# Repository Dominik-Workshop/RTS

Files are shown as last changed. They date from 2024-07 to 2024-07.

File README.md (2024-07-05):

# Linefollower

## Used tools:
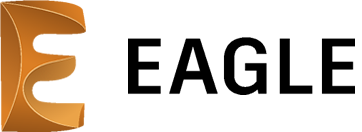
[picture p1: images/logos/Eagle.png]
 &nbsp;
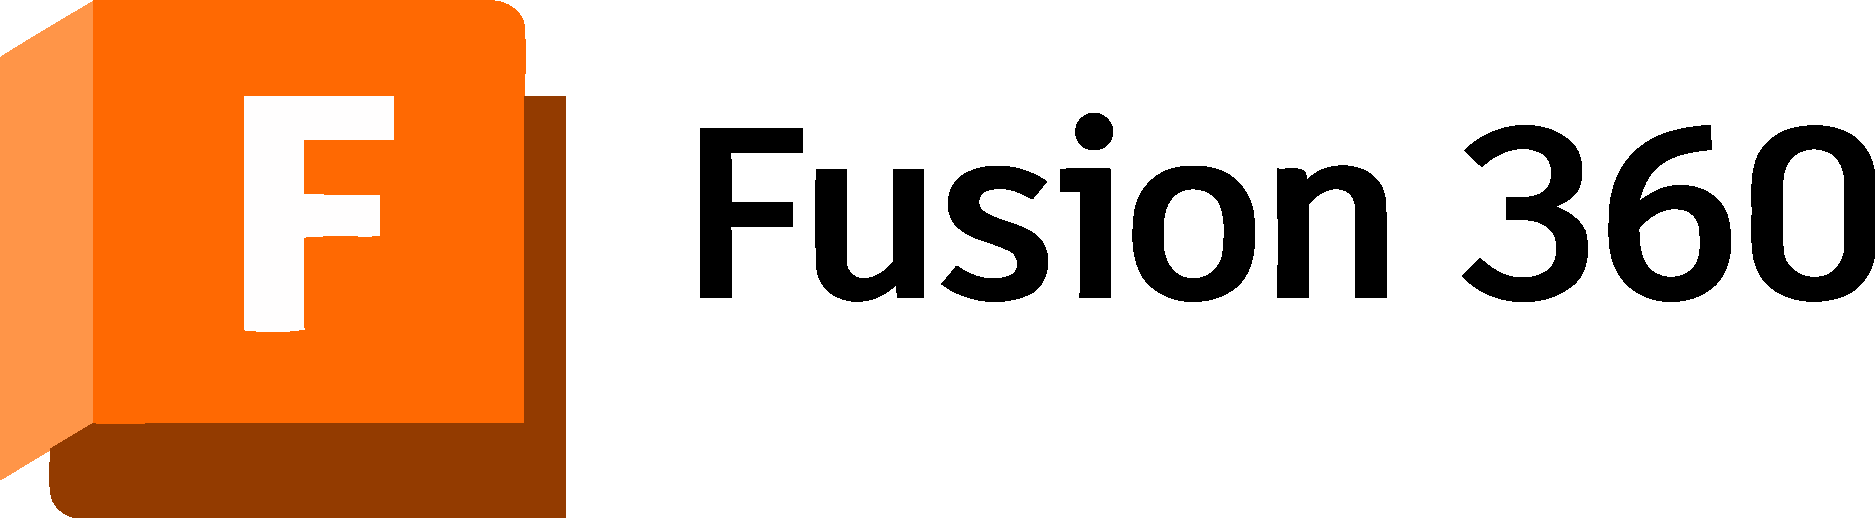
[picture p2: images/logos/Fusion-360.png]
 &nbsp;
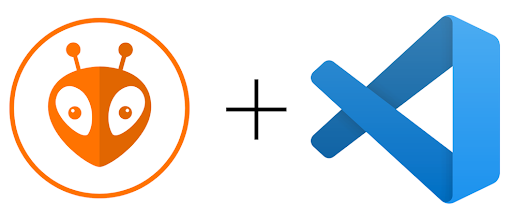
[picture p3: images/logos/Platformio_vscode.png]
 &nbsp;
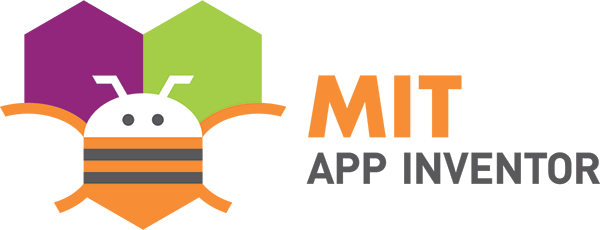
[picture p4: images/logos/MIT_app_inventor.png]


## Project overwiev
The Linefollower Robot is designed to autonomously navigate a track marked by a black line on a white surface. The goal is for the robot to complete the track as quickly as possible.
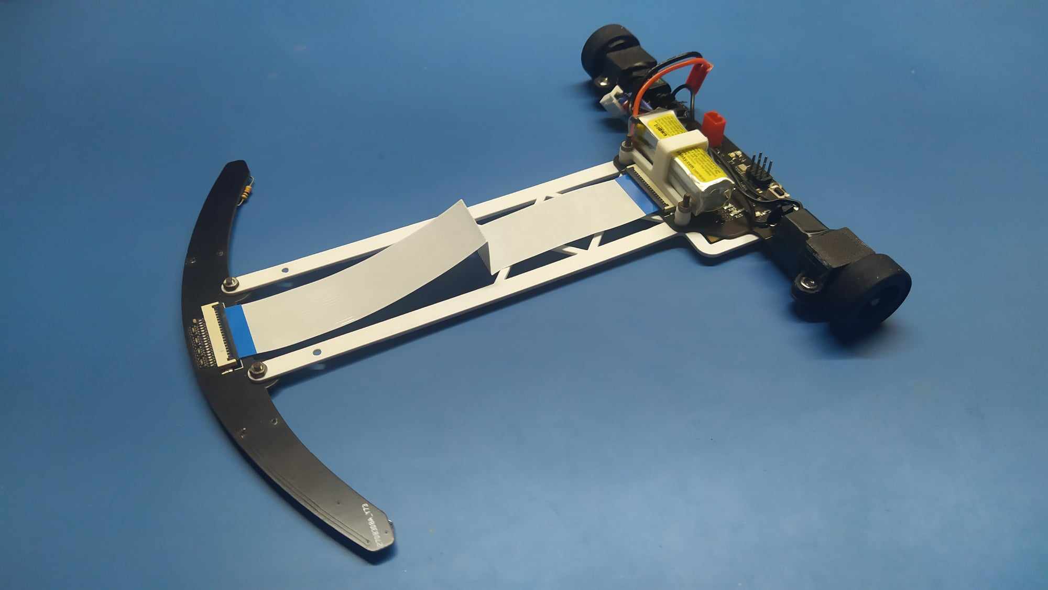
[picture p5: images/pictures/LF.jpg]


## Electronics

The robot incorporates 2 PCBs, which are connected via an FFC cable:
  - sensor board - contains 16 reflective sensors for line detection
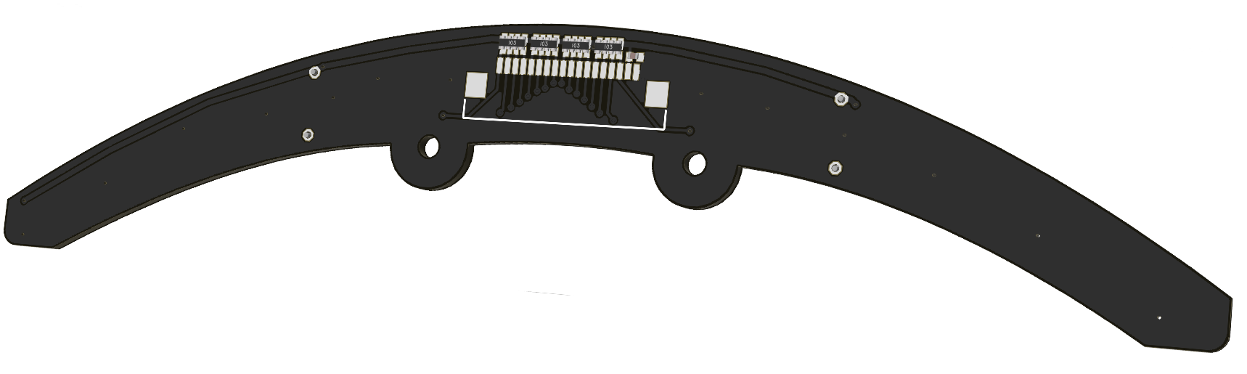
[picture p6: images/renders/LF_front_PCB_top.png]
  
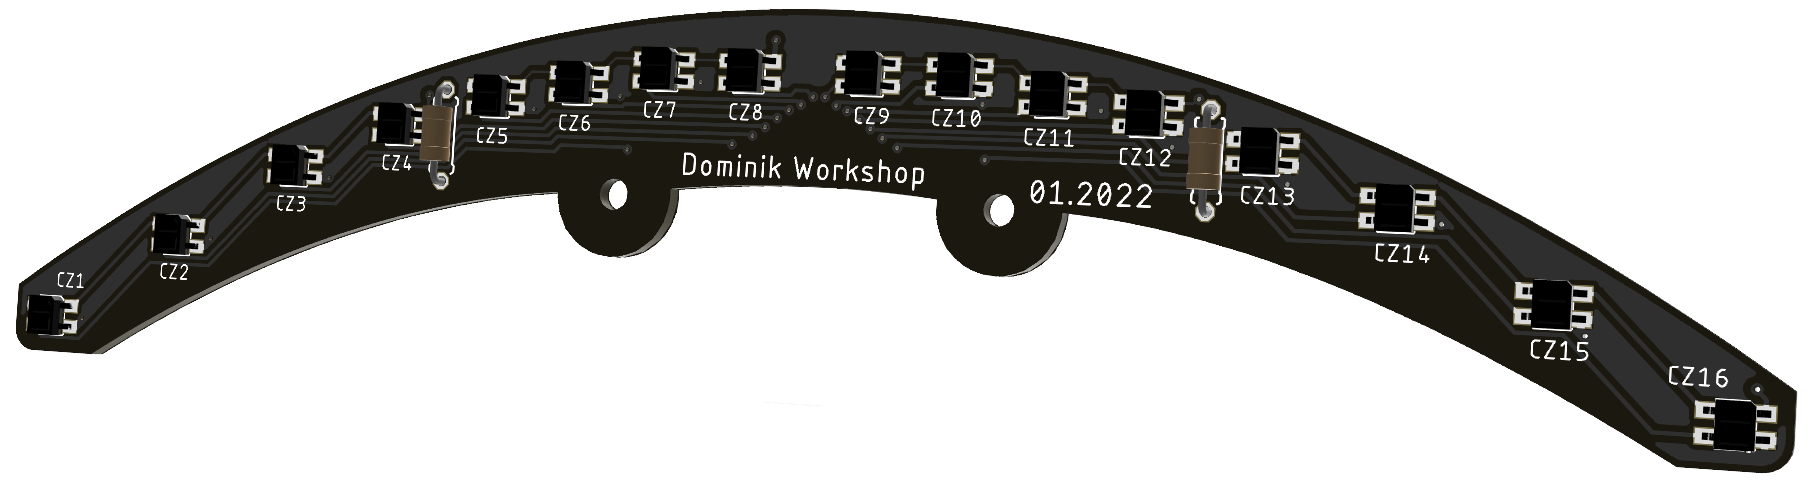
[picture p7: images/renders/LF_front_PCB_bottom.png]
  
  - main board 
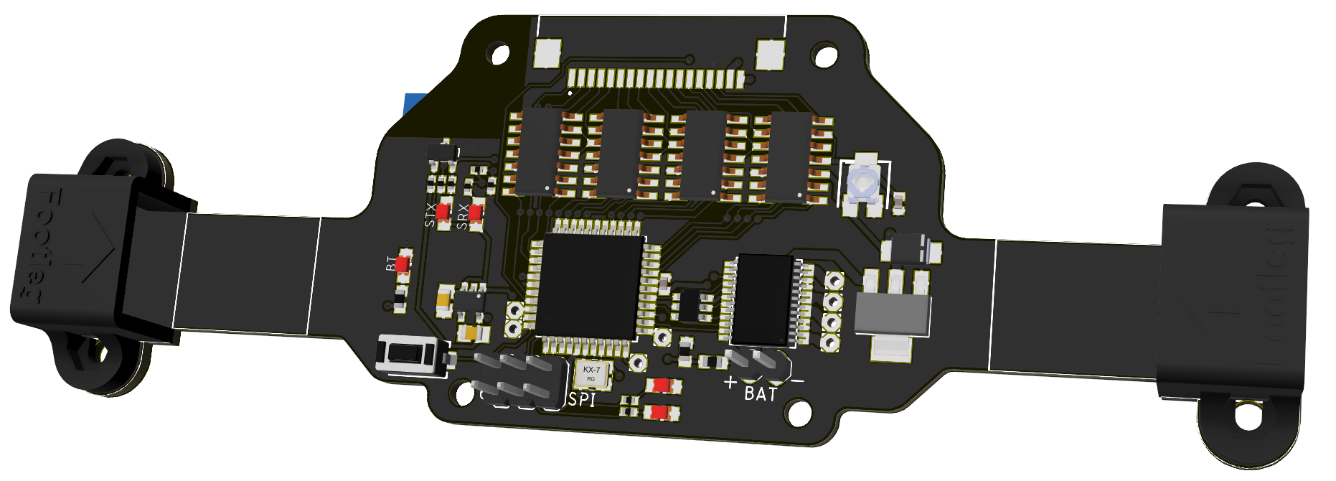
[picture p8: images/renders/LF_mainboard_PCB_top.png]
  
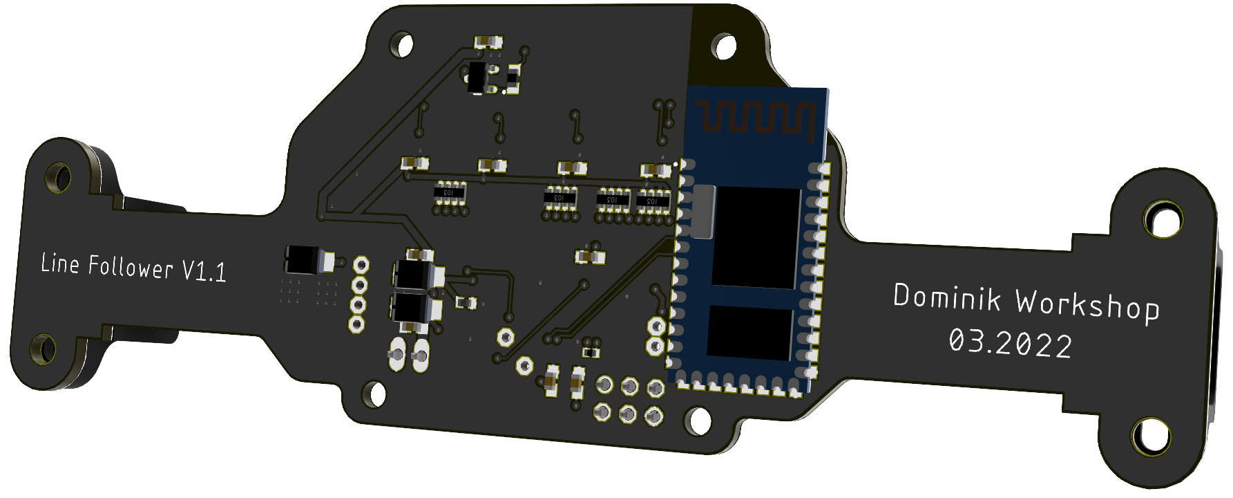
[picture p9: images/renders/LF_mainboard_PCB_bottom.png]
  

## Mechanical construction

The PCBs are mechanically joined with a lightweight 3D-printed connection bar. The motor and battery mounts are also 3D-printed.

## Android app
<p align="center">
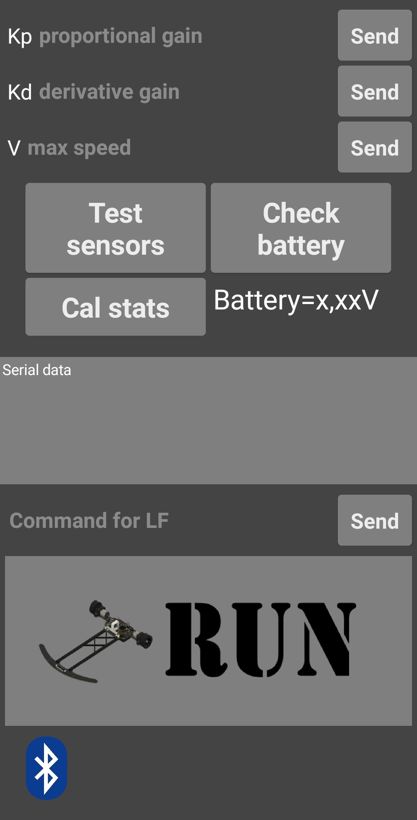
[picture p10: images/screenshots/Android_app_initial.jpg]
   &nbsp;&nbsp;
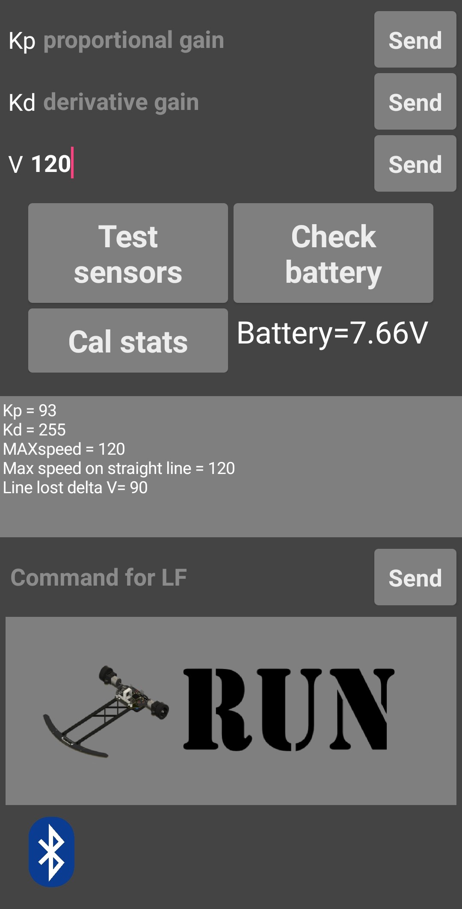
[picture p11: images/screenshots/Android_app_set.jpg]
  
</p>

## Uploading the code to the robot
If the microcontroller doesn't programm:
<details>
<summary>Click to view solution</summary>
Make sure that the fusebits are set as bellow:
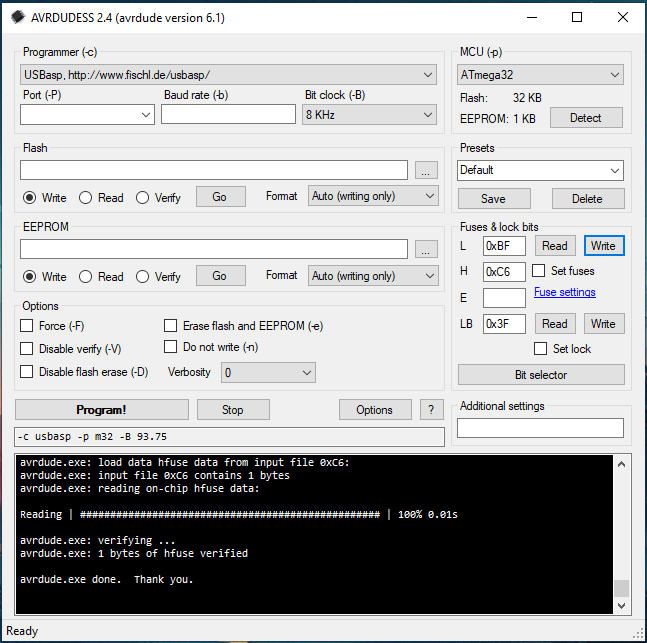
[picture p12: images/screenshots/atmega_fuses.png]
Fuse Bits Settings

</details>

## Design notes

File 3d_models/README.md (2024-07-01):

# 3D models

1. Wheel

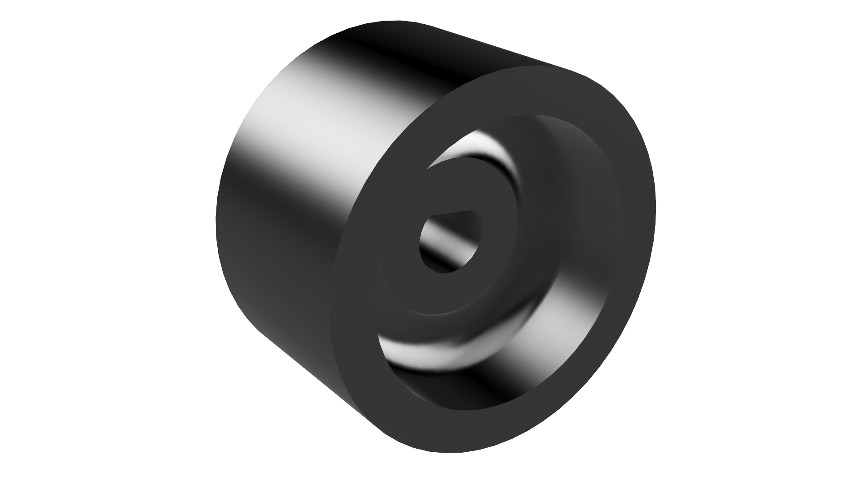
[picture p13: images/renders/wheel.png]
 

2. Battery holder

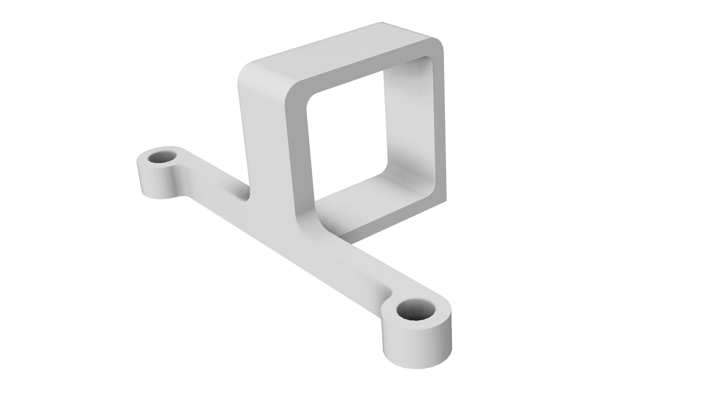
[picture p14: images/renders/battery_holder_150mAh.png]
 

3. Motor mount

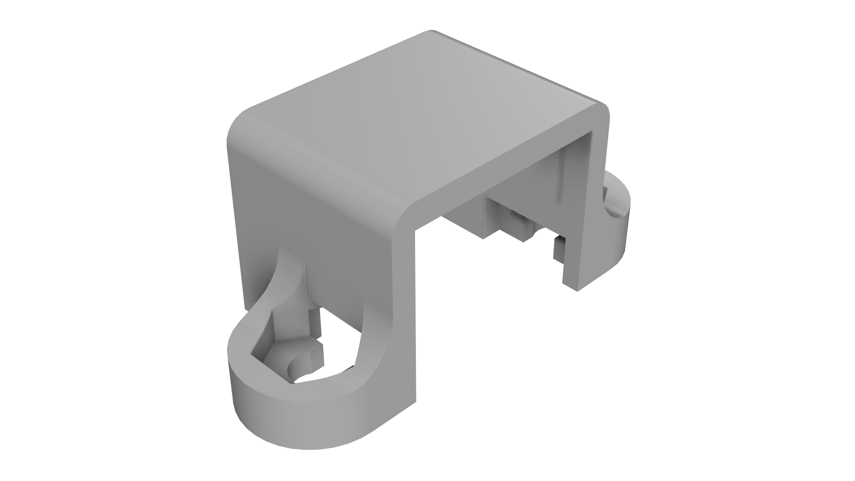
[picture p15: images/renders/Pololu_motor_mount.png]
 

4. Connection bar

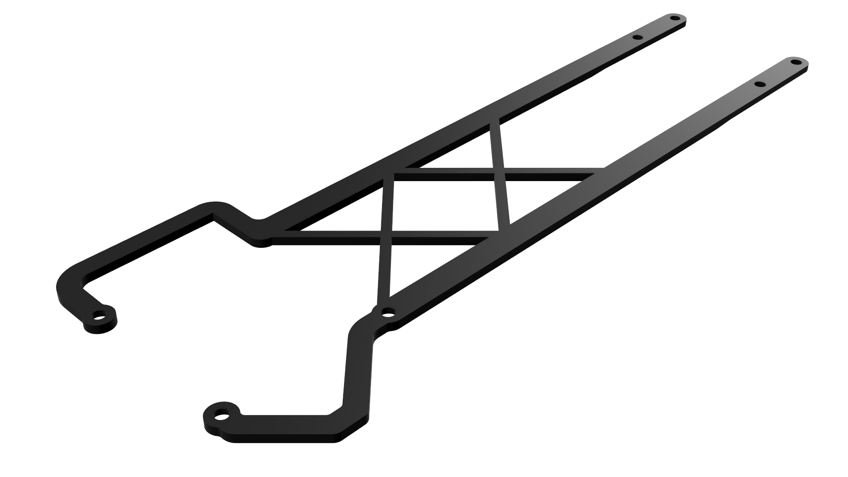
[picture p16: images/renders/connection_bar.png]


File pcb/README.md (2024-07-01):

## Main board

<p align="center">
  
</p>

## Sensor board

<p align="center">
  
</p>

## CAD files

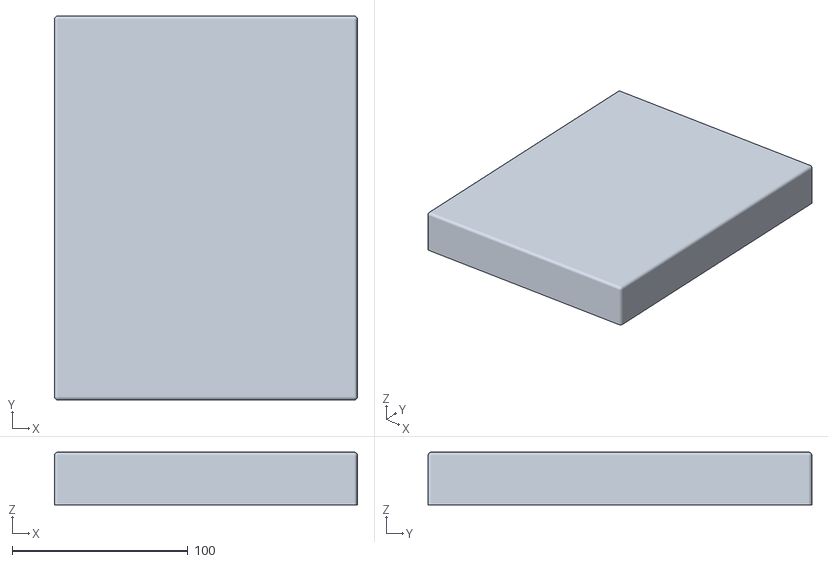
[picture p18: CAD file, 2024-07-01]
3d_models/LF_box_lid.stl
172.4 x 218.4 x 30.0

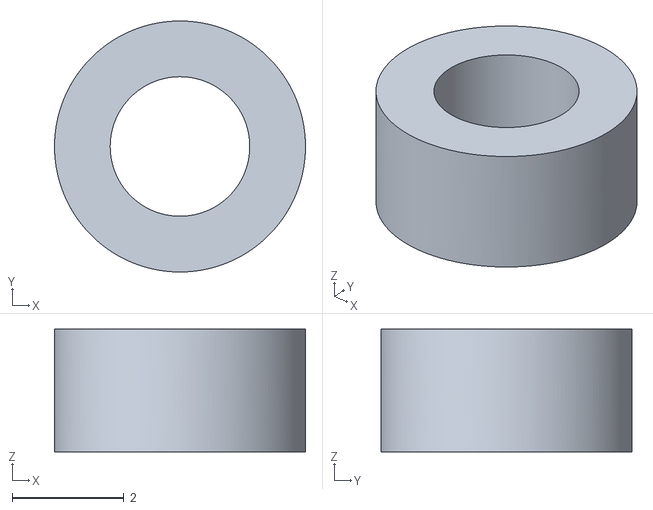
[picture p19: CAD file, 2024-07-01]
3d_models/LF_spacer.stl
4.50 x 4.50 x 2.20

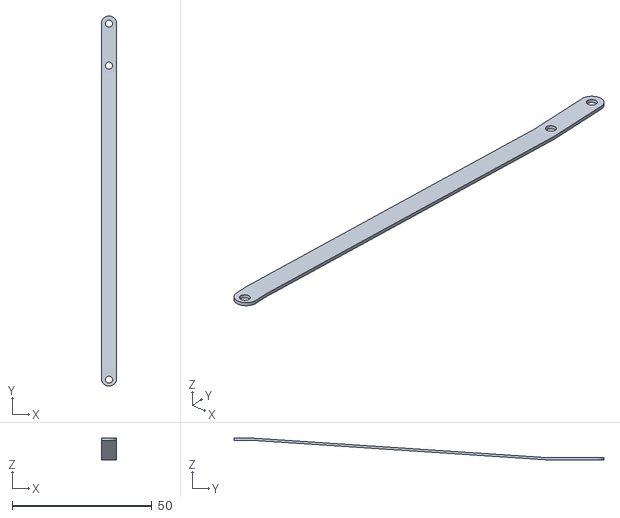
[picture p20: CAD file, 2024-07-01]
3d_models/LF_support_bar.stl
5.50 x 132.2 x 7.80

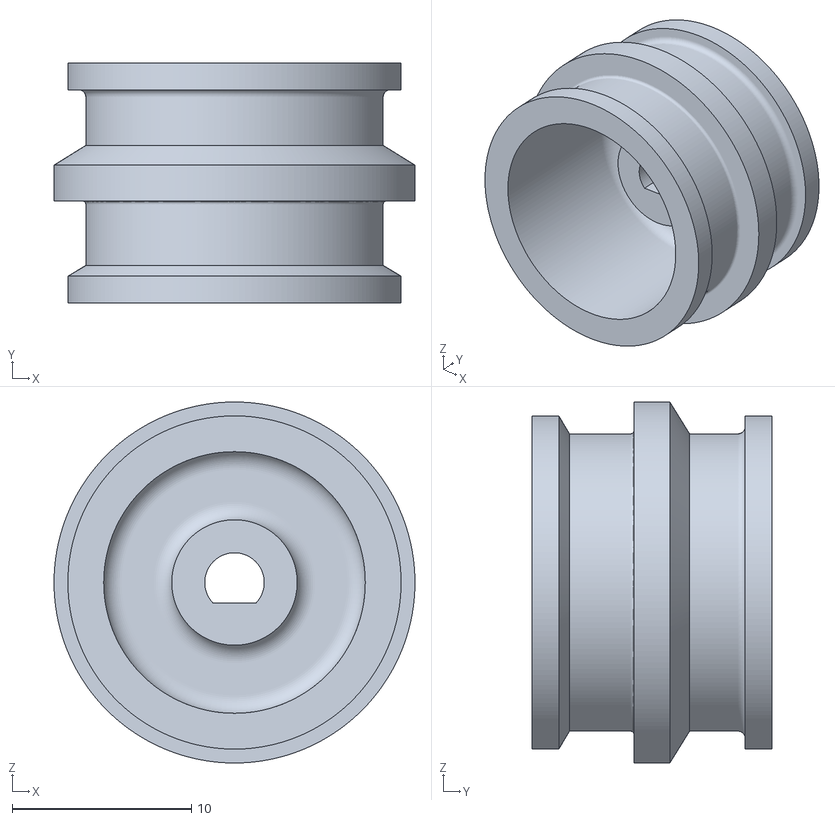
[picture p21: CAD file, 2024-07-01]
3d_models/LF_wheel_v2.stl
20.1 x 13.4 x 20.1

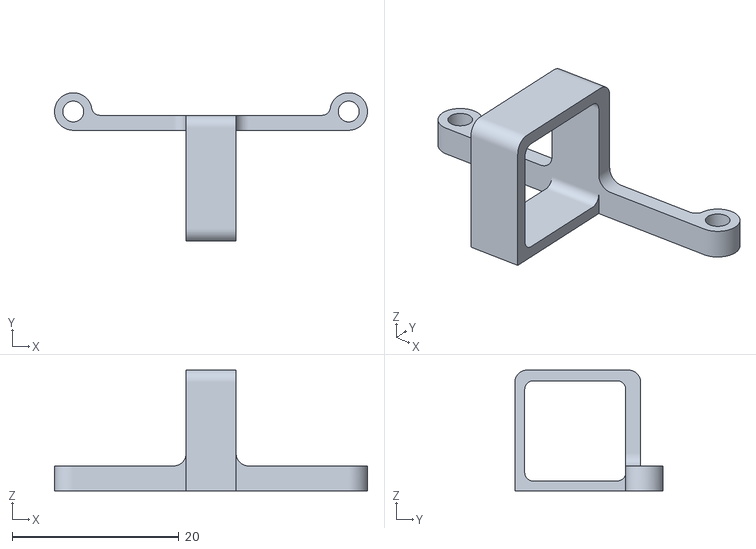
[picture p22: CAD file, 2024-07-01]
3d_models/LF_battery_holder_150mAh.stl
37.5 x 17.8 x 14.5

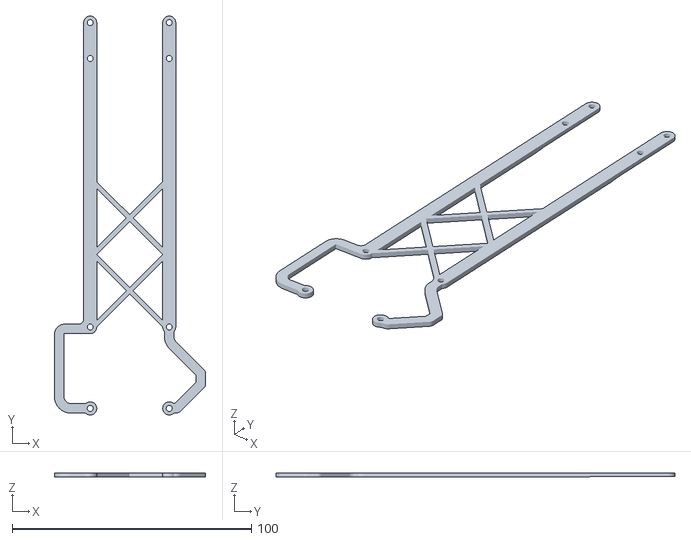
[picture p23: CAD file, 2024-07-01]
3d_models/LF_connection_bar.stl
63.2 x 166.8 x 1.80

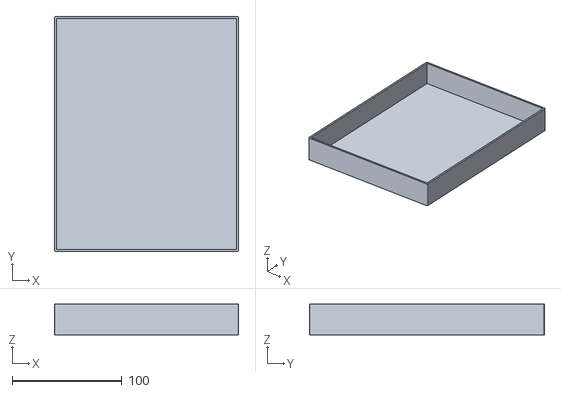
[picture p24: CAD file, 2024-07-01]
3d_models/LF_box_bottom.stl
168.0 x 214.0 x 28.0

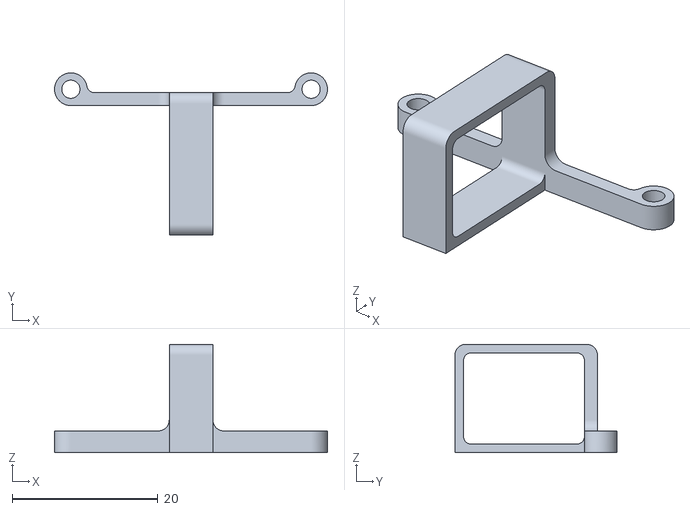
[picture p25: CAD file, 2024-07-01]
3d_models/LF_battery_holder_220mAh.stl
37.5 x 22.3 x 14.9

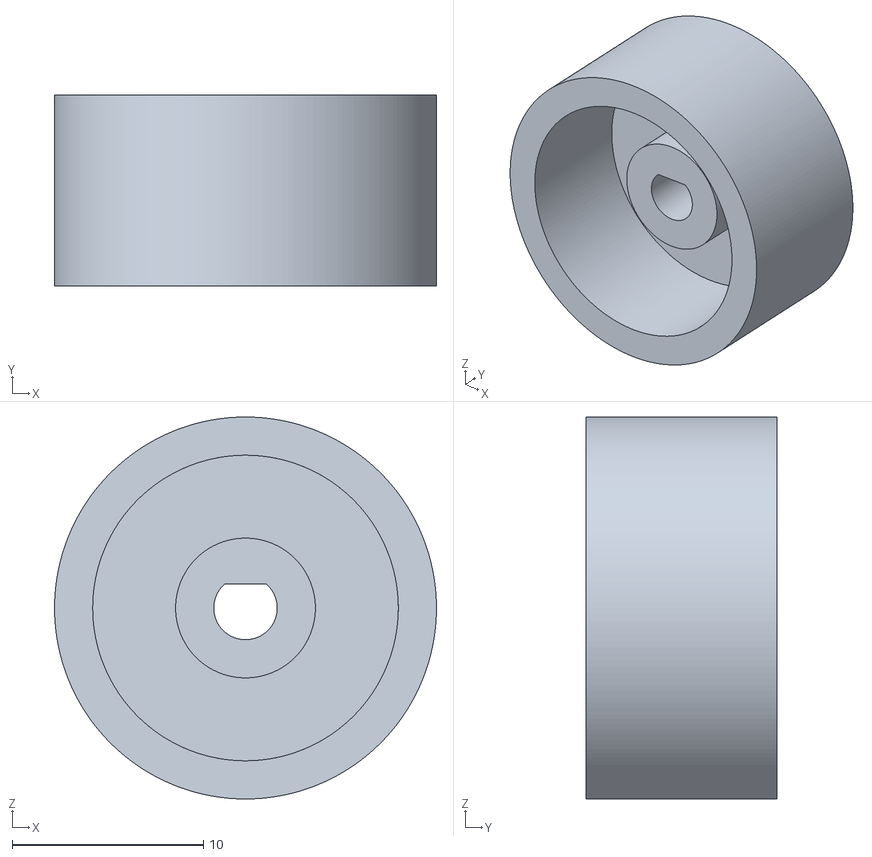
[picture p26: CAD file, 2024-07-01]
3d_models/LF_wheel.stl
20.0 x 10.0 x 20.0

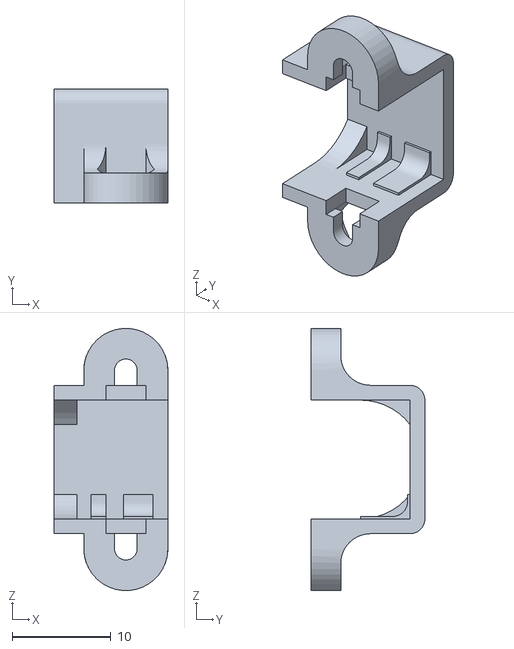
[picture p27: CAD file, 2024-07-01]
3d_models/LF_pololu_motor_holder.STL
11.5 x 11.5 x 26.5

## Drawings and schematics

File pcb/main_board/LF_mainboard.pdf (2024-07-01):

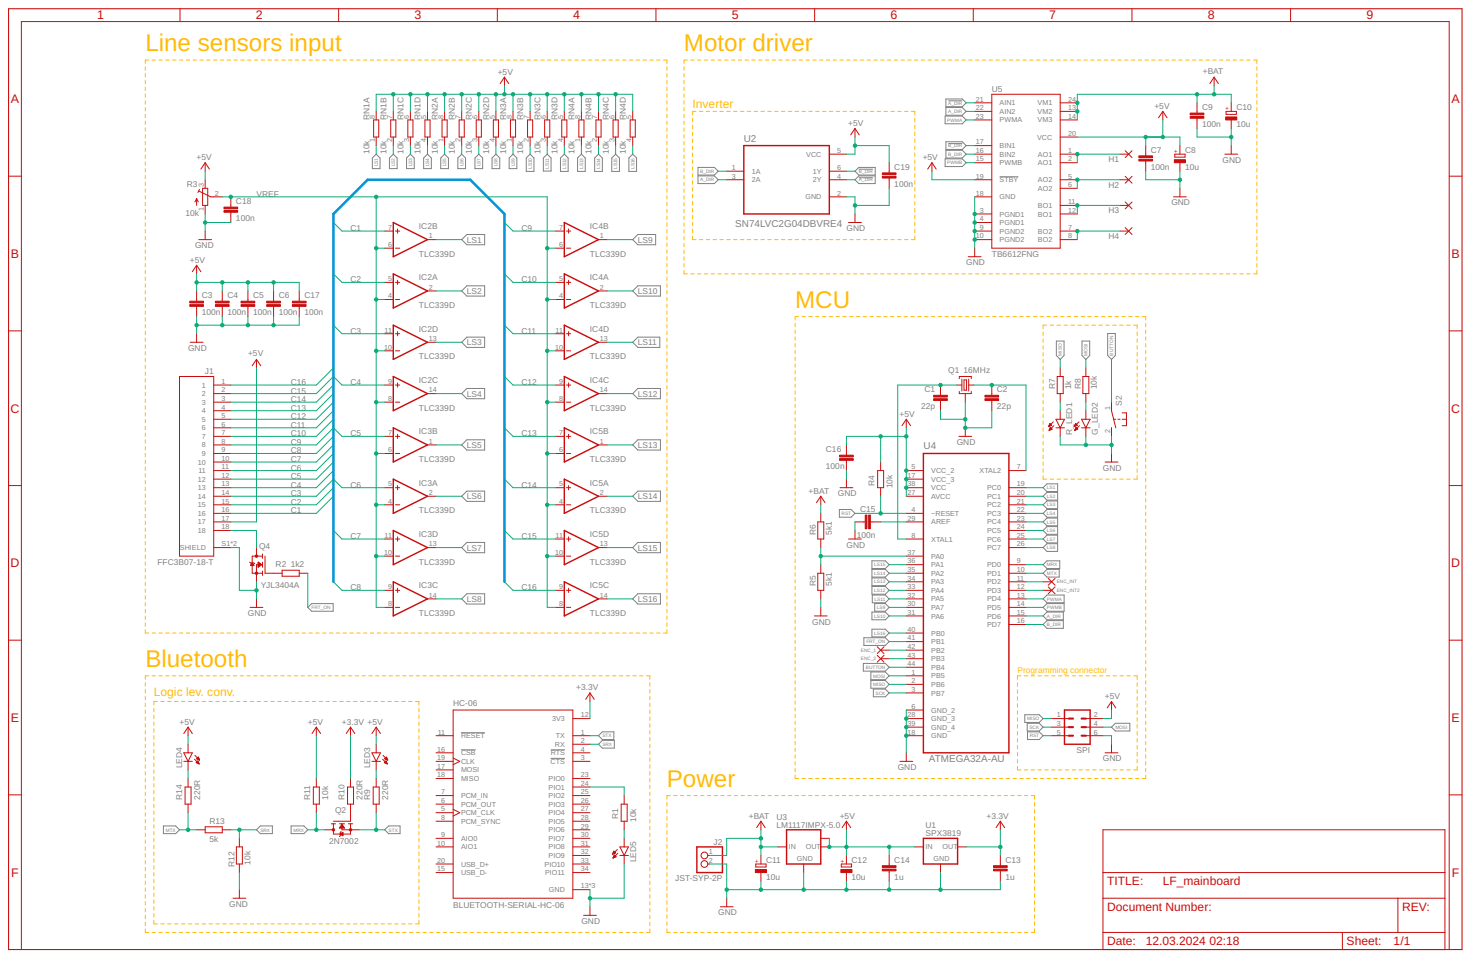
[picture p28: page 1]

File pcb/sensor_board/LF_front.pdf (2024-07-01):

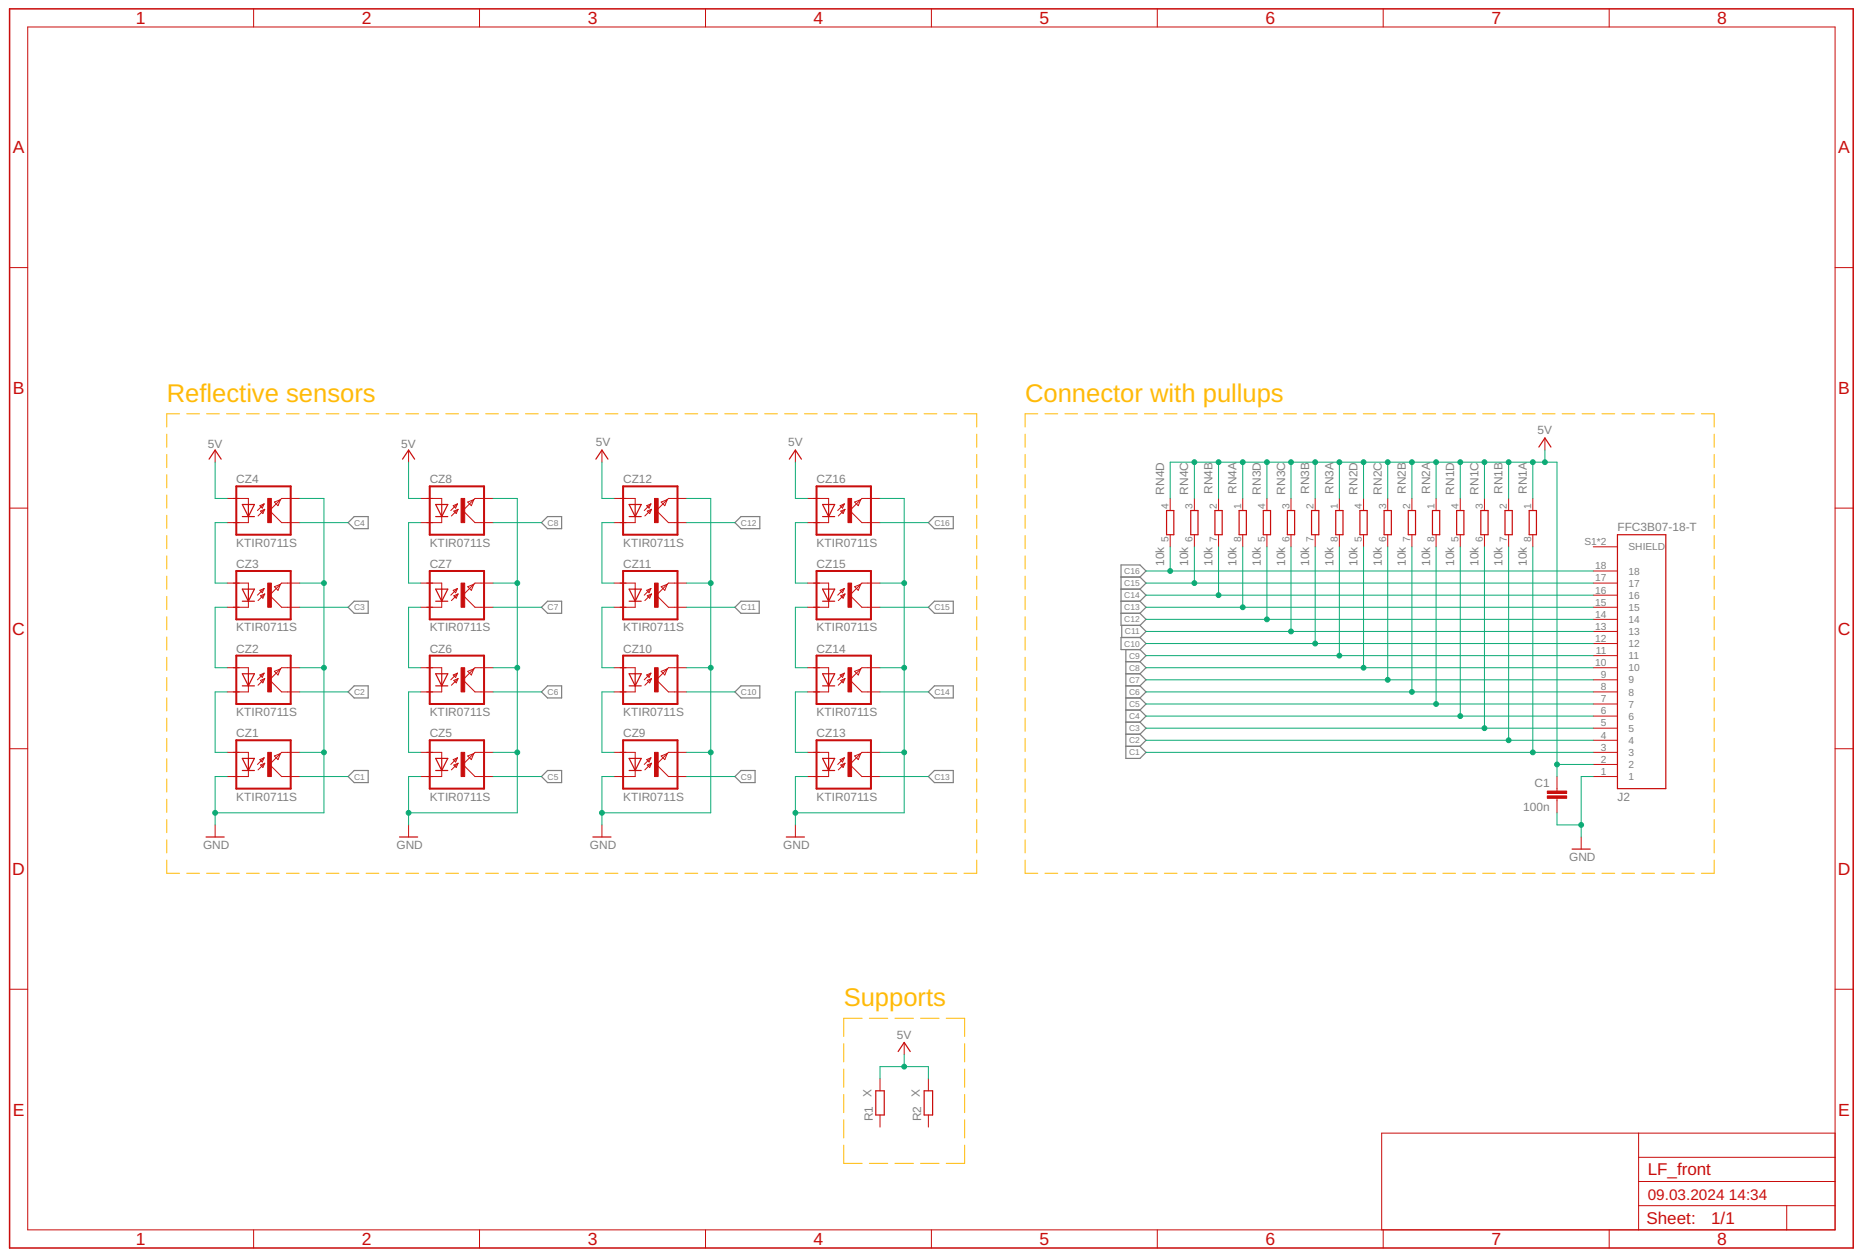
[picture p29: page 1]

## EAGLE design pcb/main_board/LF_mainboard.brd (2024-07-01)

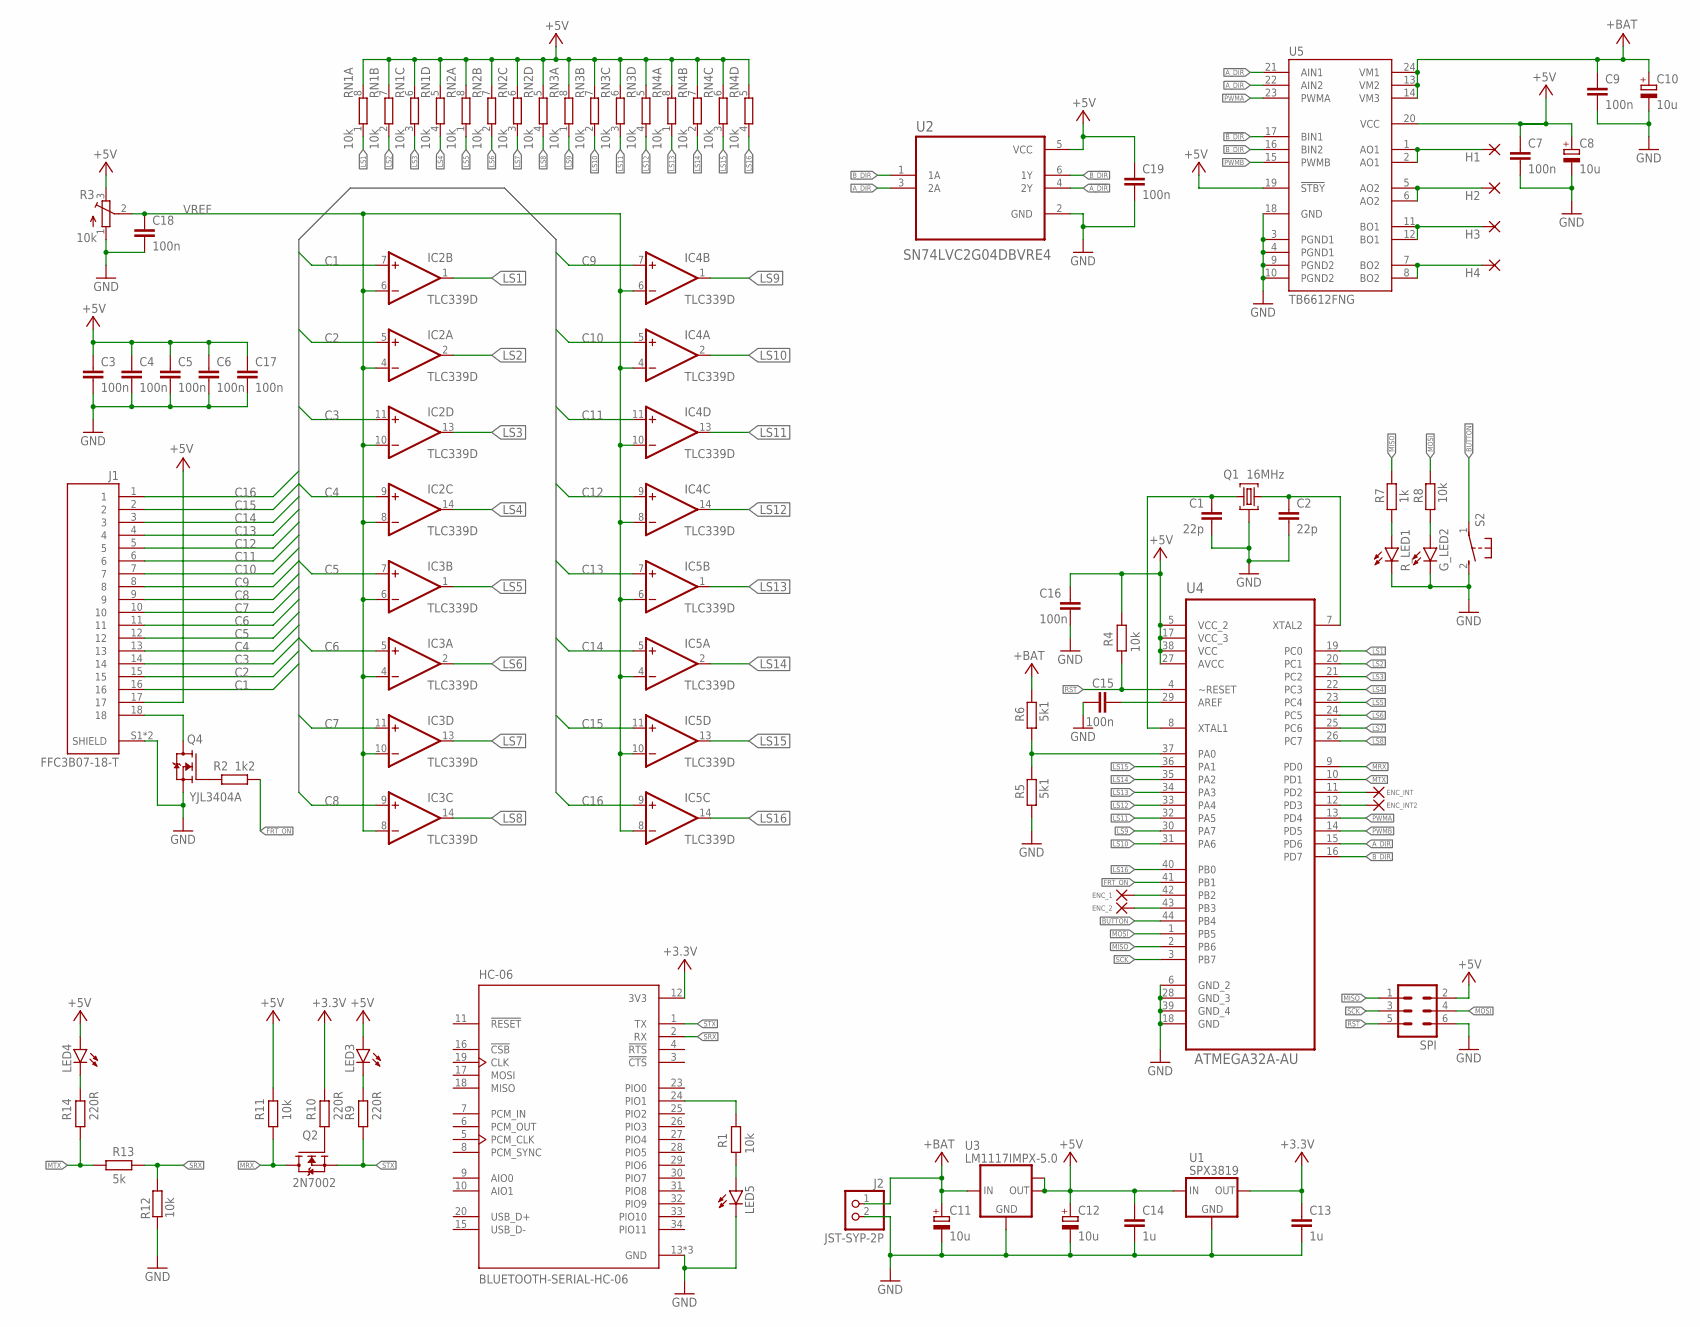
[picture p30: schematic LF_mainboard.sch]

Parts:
C1, C2: 22p; C0603
C3, C4, C5, C6, C7, C9, C15, C17: 100n; C0603
C8, C10, C11, C12: 10u; B/3528-21W
C13, C14: 1u; C0805
C16, C18, C19: 100n; C0402
ENC_2: 1,6/0,8
G_LED2: LEDCHIP-LED0805; CHIP-LED0805
H1, H2, H3, H4, H5, H6, H8: 1,6/0,8
HC-06: BLUETOOTH-SERIAL-HC-06; XCVR_BLUETOOTH-SERIAL-HC-06
IC2, IC3, IC4, IC5: TLC339D; SO14
J1: FFC3B07-18-T; GCT_FFC3B07-18-T
J2: JST-SYP-2P; 1X02
LED3, LED4, LED5: LEDCHIP-LED0805; CHIP-LED0805
Q1: 16MHz; CRYSTAL_3,4X2,7
Q2: 2N7002; SOT95P240X111-3N
Q4: YJL3404A; SOT95P240X111-3N
R1: 10k; R0603
R2: 1k2; R0603
R3: 10k; SM-42/43A
R4, R8, R11, R12: 10k; R0402
R5, R6: 5k1; R0603
R7: 1k; R0402
R9, R10, R14: 220R; R0402
R13: 5k; R0402
RN1, RN2, RN3, RN4: 10k; CAT16
R_LED1: LEDCHIP-LED0805; CHIP-LED0805
S2: DTSM-3
SPI: MA03-2
U1: SPX3819; SOT23-5
U2: SN74LVC2G04DBVRE4; SOT95P280X145-6N
U3: LM1117IMPX-5.0; SOT223
U4: ATMEGA32A-AU; QFP80P1200X1200X120-44N
U5: TB6612FNG; SSOP24

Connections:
!A_DIR: U2.4 (2Y), U5.21 (AIN1)
!B_DIR: U2.6 (1Y), U5.17 (BIN1)
+3.3V: C13.1, HC-06.12 (3V3), R10.2, U1.5 (OUT)
+5V: C3.1, C4.1, C5.1, C6.1, C7.1, C8.+, C12.+, C14.1, C16.1, C17.1, C19.1, IC2.3 (V+), IC3.3 (V+), IC4.3 (V+), IC5.3 (V+), J1.17, LED3.A, LED4.A, R3.3 (E), R4.2, R11.2, RN1.5 (2), RN1.6 (2), RN1.7 (2), RN1.8 (2), RN2.5 (2), RN2.6 (2), RN2.7 (2), RN2.8 (2), RN3.5 (2), RN3.6 (2), RN3.7 (2), RN3.8 (2), RN4.5 (2), RN4.6 (2), RN4.7 (2), RN4.8 (2), SPI.2, U1.1 (IN), U1.3 (IN), U2.5 (VCC), U3.2 (OUT), U3.TAB (OUT1), U4.5 (VCC_2), U4.17 (VCC_3), U4.27 (AVCC), U4.38 (VCC), U5.19 (!STBY), U5.20 (VCC)
+BAT: C9.1, C10.+, C11.+, J2.1, R6.2, U3.3 (IN), U5.13 (VM2), U5.14 (VM3), U5.24 (VM1)
AO: H1.1, U5.1 (AO1), U5.2 (AO1)
AO2: H2.1, U5.5 (AO2), U5.6 (AO2)
AREF: C15.2, U4.29 (AREF)
A_DIR: U2.3 (2A), U4.15 (PD6), U5.22 (AIN2)
BAT_MEAS: R5.2, R6.1, U4.37 (PA0)
BO1: H3.1, U5.11 (BO1), U5.12 (BO1)
BO2: H4.1, U5.7 (BO2), U5.8 (BO2)
BUTTON: S2.1, U4.44 (PB4)
B_DIR: U2.1 (1A), U4.16 (PD7), U5.16 (BIN2)
C1: IC2.7 (+IN), J1.16
C2: IC2.5 (+IN), J1.15
C3: IC2.11 (+IN), J1.14
C4: IC2.9 (+IN), J1.13
C5: IC3.7 (+IN), J1.12
C6: IC3.5 (+IN), J1.11
C7: IC3.11 (+IN), J1.10
C8: IC3.9 (+IN), J1.9
C9: IC4.7 (+IN), J1.8
C10: IC4.5 (+IN), J1.7
C11: IC4.11 (+IN), J1.6
C12: IC4.9 (+IN), J1.5
C13: IC5.7 (+IN), J1.4
C14: IC5.5 (+IN), J1.3
C15: IC5.11 (+IN), J1.2
C16: IC5.9 (+IN), J1.1
ENC_1: H8.1, U4.42 (PB2)
ENC_2: ENC_2.1, U4.43 (PB3)
ENC_INT: H5.1, U4.11 (PD2)
ENC_INT2: H6.1, U4.12 (PD3)
FRT_ON: R2.1, U4.41 (PB1)
GND: C1.2, C2.2, C3.2, C4.2, C5.2, C6.2, C7.2, C8.-, C9.2, C10.-, C11.-, C12.-, C13.2, C14.2, C15.1, C16.2, C17.2, C18.2, C19.2, G_LED2.C, HC-06.13 (GND), HC-06.21 (GND), HC-06.22 (GND), IC2.12 (V-), IC3.12 (V-), IC4.12 (V-), IC5.12 (V-), J1.S1 (SHIELD), J1.S2 (SHIELD), J2.2, LED5.C, Q1.GND (2), Q1.GND2 (2), Q4.2 (S), R3.1 (A), R5.1, R12.2, R_LED1.C, S2.2, SPI.6, U1.2 (GND), U2.2 (GND), U3.1 (GND), U4.6 (GND_2), U4.18 (GND), U4.28 (GND_3), U4.39 (GND_4), U5.3 (PGND1), U5.4 (PGND1), U5.9 (PGND2), U5.10 (PGND2), U5.18 (GND)
LED1: R7.1, R_LED1.A
LED2: G_LED2.A, R8.1
LS1: IC2.1 (OUT), RN1.1, U4.19 (PC0)
LS2: IC2.2 (OUT), RN1.2 (1), U4.20 (PC1)
LS3: IC2.13 (OUT), RN1.3 (1), U4.21 (PC2)
LS4: IC2.14 (OUT), RN1.4 (1), U4.22 (PC3)
LS5: IC3.1 (OUT), RN2.1, U4.23 (PC4)
LS6: IC3.2 (OUT), RN2.2 (1), U4.24 (PC5)
LS7: IC3.13 (OUT), RN2.3 (1), U4.25 (PC6)
LS8: IC3.14 (OUT), RN2.4 (1), U4.26 (PC7)
LS9: IC4.1 (OUT), RN3.1, U4.30 (PA7)
LS10: IC4.2 (OUT), RN3.2 (1), U4.31 (PA6)
LS11: IC4.13 (OUT), RN3.3 (1), U4.32 (PA5)
LS12: IC4.14 (OUT), RN3.4 (1), U4.33 (PA4)
LS13: IC5.1 (OUT), RN4.1, U4.34 (PA3)
LS14: IC5.2 (OUT), RN4.2 (1), U4.35 (PA2)
LS15: IC5.13 (OUT), RN4.3 (1), U4.36 (PA1)
LS16: IC5.14 (OUT), RN4.4 (1), U4.40 (PB0)
MISO: R7.2, SPI.1, U4.2 (PB6)
MOSI: R8.2, SPI.4, U4.1 (PB5)
MRX: Q2.3 (D), R11.1, U4.9 (PD0)
MTX: R13.1, R14.1, U4.10 (PD1)
unnamed: C1.1, Q1.CRST1 (1), U4.8 (XTAL1)
unnamed: C2.1, Q1.CRST2 (3), U4.7 (XTAL2)
unnamed: J1.18, Q4.3 (D)
unnamed: Q4.1 (G), R2.2
unnamed: HC-06.24 (PIO1), R1.2
unnamed: Q2.1 (G), R10.1
unnamed: LED4.C, R14.2
unnamed: LED3.C, R9.2
unnamed: LED5.A, R1.1
PWMA: U4.13 (PD4), U5.23 (PWMA)
PWMB: U4.14 (PD5), U5.15 (PWMB)
RST: R4.1, SPI.5, U4.4 (~RESET)
SCK: SPI.3, U4.3 (PB7)
SRX: HC-06.2 (RX), R12.1, R13.2
STX: HC-06.1 (TX), Q2.2 (S), R9.1
VREF: C18.1, IC2.4 (-IN), IC2.6 (-IN), IC2.8 (-IN), IC2.10 (-IN), IC3.4 (-IN), IC3.6 (-IN), IC3.8 (-IN), IC3.10 (-IN), IC4.4 (-IN), IC4.6 (-IN), IC4.8 (-IN), IC4.10 (-IN), IC5.4 (-IN), IC5.6 (-IN), IC5.8 (-IN), IC5.10 (-IN), R3.2 (S)

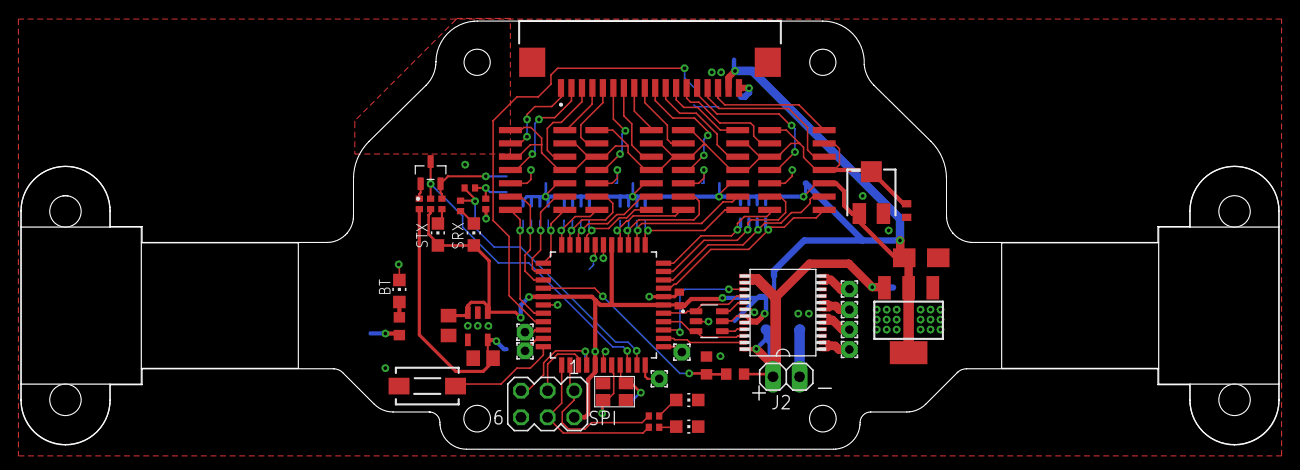
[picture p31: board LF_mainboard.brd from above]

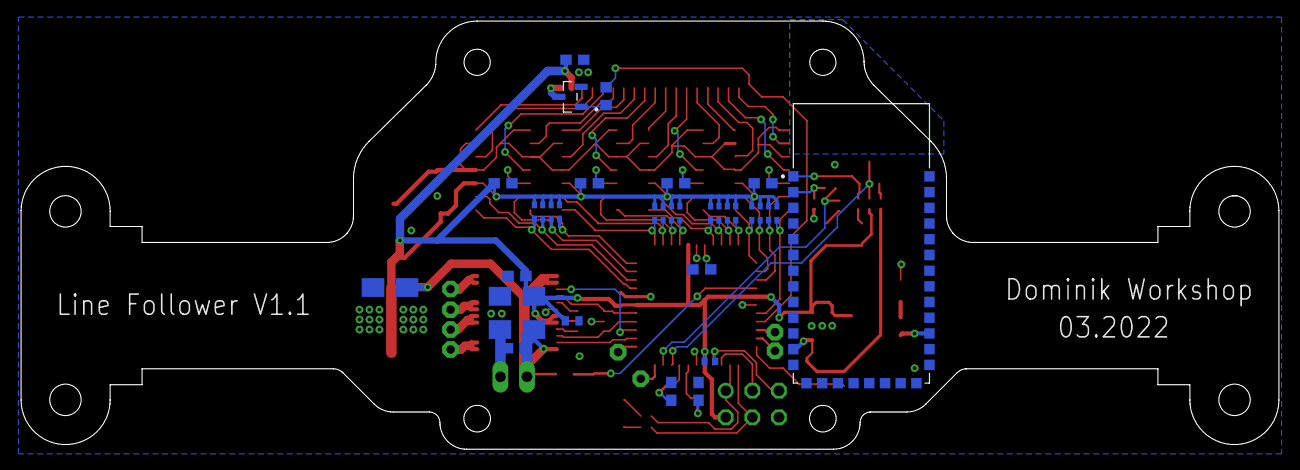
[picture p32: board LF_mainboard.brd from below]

Board: 2 copper layers, 120.1 x 40.9 mm, 69 parts (22 on the bottom side), 74 nets.

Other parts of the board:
U$1, U$2: HP_NM

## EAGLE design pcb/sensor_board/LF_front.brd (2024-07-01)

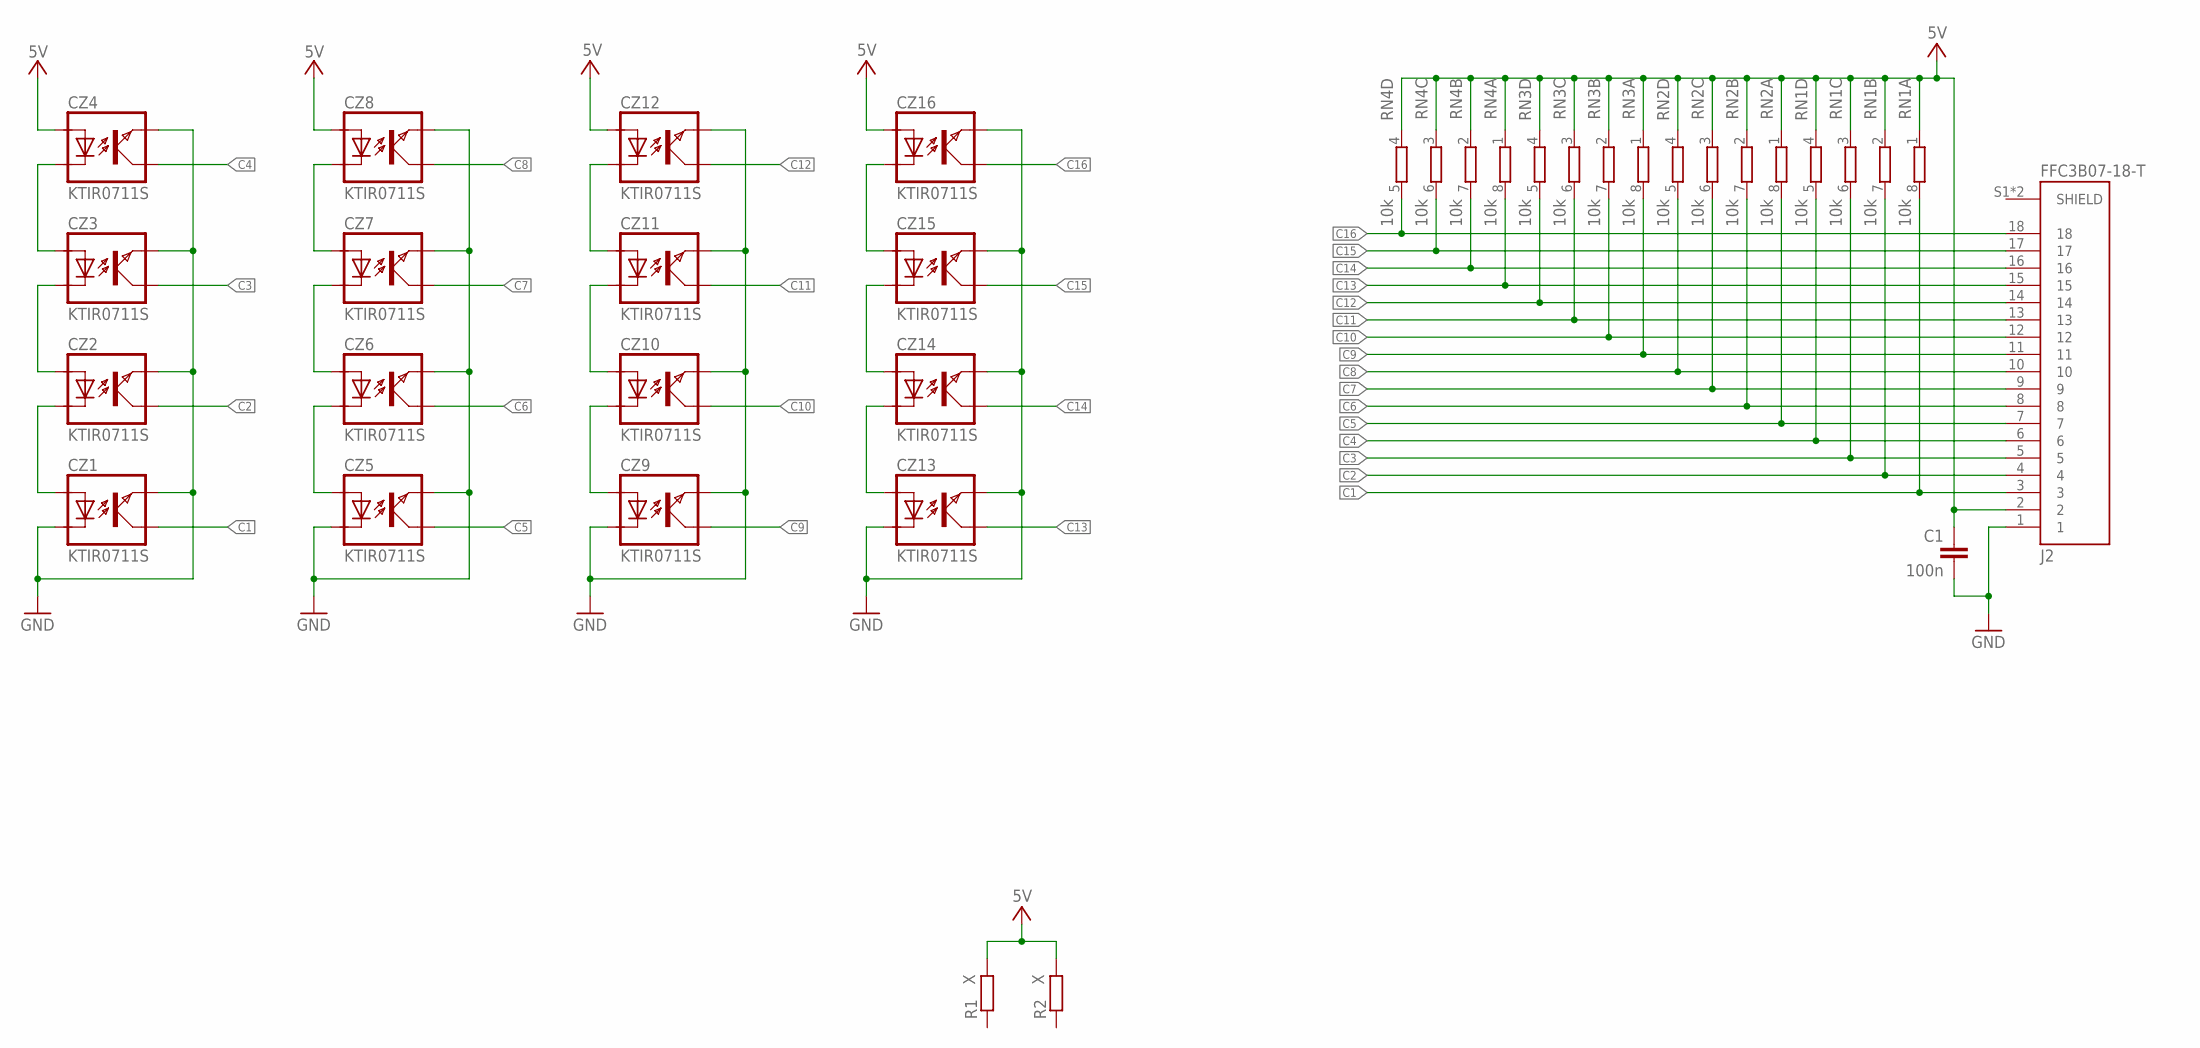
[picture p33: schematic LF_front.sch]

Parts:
C1: 100n; C0402
CZ1, CZ2, CZ3, CZ4, CZ5, CZ6, CZ7, CZ8, CZ9, CZ10, CZ11, CZ12, CZ13, CZ14, CZ15, CZ16: KTIR0711S; TOP
J2: FFC3B07-18-T; GCT_FFC3B07-18-T
R1, R2: X; 0207/7
RN1, RN2, RN3, RN4: 10k; EXB38V

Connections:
5V: C1.2, CZ4.ANODA, CZ8.ANODA, CZ12.ANODA, CZ16.ANODA, J2.2, R1.2, R2.2, RN1.1, RN1.2 (1), RN1.3 (1), RN1.4 (1), RN2.1, RN2.2 (1), RN2.3 (1), RN2.4 (1), RN3.1, RN3.2 (1), RN3.3 (1), RN3.4 (1), RN4.1, RN4.2 (1), RN4.3 (1), RN4.4 (1)
C1: CZ1.KOLEKTOR, J2.3, RN1.8 (2)
C2: CZ2.KOLEKTOR, J2.4, RN1.7 (2)
C3: CZ3.KOLEKTOR, J2.5, RN1.6 (2)
C4: CZ4.KOLEKTOR, J2.6, RN1.5 (2)
C5: CZ5.KOLEKTOR, J2.7, RN2.8 (2)
C6: CZ6.KOLEKTOR, J2.8, RN2.7 (2)
C7: CZ7.KOLEKTOR, J2.9, RN2.6 (2)
C8: CZ8.KOLEKTOR, J2.10, RN2.5 (2)
C9: CZ9.KOLEKTOR, J2.11, RN3.8 (2)
C10: CZ10.KOLEKTOR, J2.12, RN3.7 (2)
C11: CZ11.KOLEKTOR, J2.13, RN3.6 (2)
C12: CZ12.KOLEKTOR, J2.14, RN3.5 (2)
C13: CZ13.KOLEKTOR, J2.15, RN4.8 (2)
C14: CZ14.KOLEKTOR, J2.16, RN4.7 (2)
C15: CZ15.KOLEKTOR, J2.17, RN4.6 (2)
C16: CZ16.KOLEKTOR, J2.18, RN4.5 (2)
GND: C1.1, CZ1.EMITER, CZ1.KATODA, CZ2.EMITER, CZ3.EMITER, CZ4.EMITER, CZ5.EMITER, CZ5.KATODA, CZ6.EMITER, CZ7.EMITER, CZ8.EMITER, CZ9.EMITER, CZ9.KATODA, CZ10.EMITER, CZ11.EMITER, CZ12.EMITER, CZ13.EMITER, CZ13.KATODA, CZ14.EMITER, CZ15.EMITER, CZ16.EMITER, J2.1
unnamed: CZ1.ANODA, CZ2.KATODA
unnamed: CZ2.ANODA, CZ3.KATODA
unnamed: CZ3.ANODA, CZ4.KATODA
unnamed: CZ15.ANODA, CZ16.KATODA
unnamed: CZ14.ANODA, CZ15.KATODA
unnamed: CZ13.ANODA, CZ14.KATODA
unnamed: CZ11.ANODA, CZ12.KATODA
unnamed: CZ10.ANODA, CZ11.KATODA
unnamed: CZ9.ANODA, CZ10.KATODA
unnamed: CZ5.ANODA, CZ6.KATODA
unnamed: CZ6.ANODA, CZ7.KATODA
unnamed: CZ7.ANODA, CZ8.KATODA

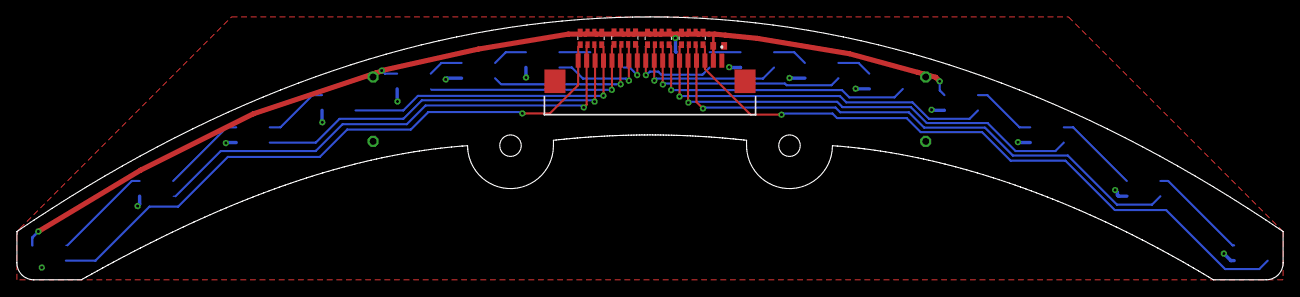
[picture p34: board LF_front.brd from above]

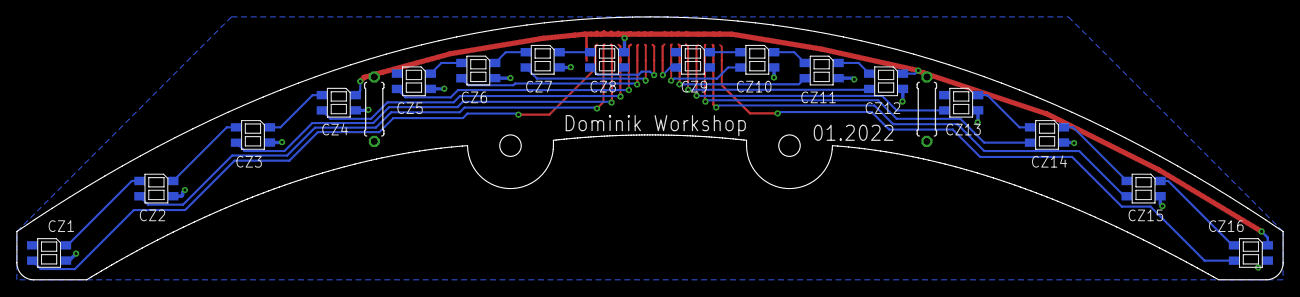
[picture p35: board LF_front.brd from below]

Board: 2 copper layers, 149.9 x 31.1 mm, 24 parts (18 on the bottom side), 30 nets.

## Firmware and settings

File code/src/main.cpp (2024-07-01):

/**
 * @file main.cpp
 * @author Dominik Workshop
 * @brief 
 * @version 0.1
 * @date 2024-03-30
 * 
 * @copyright Copyright (c) 2024
 * 
 */

#include <Arduino.h>

#include "linefollower.hh"

int main() {

  init();   // Arduino function, initializes peripherals

  Serial.begin(9600);

  Linefollower linefollower;

  while(1){
    linefollower.battery.checkVoltage();
    if(digitalRead(BUTTON) == LOW)
      linefollower.spinWheelsForCleaning();

    if(Serial.available()>0){
      char data = Serial.read();
      switch(data){
        case 'B':
          linefollower.battery.sendVoltage();
          break;
        case 't': 
          linefollower.lineSensors.test();
          break;
        case 'D': 
          linefollower.driveOnLine();
          break;
        case 'c':
          linefollower.calibration();
          break;  
        case 0x0A:
          break;
        case 0x0D:
          break;
        default : 
          Serial.println("Incorrect option");
          break;
        }
    }
  }
} 

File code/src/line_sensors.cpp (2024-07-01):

/**
 * @file line_sensors.cpp
 * @author Dominik Workshop
 * @brief 
 * @version 0.1
 * @date 2024-03-30
 * 
 * @copyright Copyright (c) 2024
 * 
 */

#include "line_sensors.hh"

LineSensors::LineSensors(){
  pinMode(FRONT_POWER, OUTPUT);
  digitalWrite(FRONT_POWER, LOW);

  pinMode(CZ1, INPUT);
  pinMode(CZ2, INPUT);
  pinMode(CZ3, INPUT);
  pinMode(CZ4, INPUT);
  pinMode(CZ5, INPUT);
  pinMode(CZ6, INPUT);
  pinMode(CZ7, INPUT);
  pinMode(CZ8, INPUT);
  pinMode(CZ9, INPUT);
  pinMode(CZ10, INPUT);
  pinMode(CZ11, INPUT);
  pinMode(CZ12, INPUT);
  pinMode(CZ13, INPUT);
  pinMode(CZ14, INPUT);
  pinMode(CZ15, INPUT);
  pinMode(CZ16, INPUT);
}

void LineSensors::readSensors(){
  #ifdef NEGATIVE
  sensorReadings[0] = !(PINC & B00000001);            //CZ1
  sensorReadings[1] = !(PINC >> 1 & B00000010 >> 1);  //CZ2
  sensorReadings[2] = !(PINC >> 2 & B00000100 >> 2);  //CZ3
  sensorReadings[3] = !(PINC >> 3 & B00001000 >> 3);  //CZ4
  sensorReadings[4] = !(PINC >> 4 & B00010000 >> 4);  //CZ5
  sensorReadings[5] = !(PINC >> 5 & B00100000 >> 5);  //CZ6
  sensorReadings[6] = !(PINC >> 6 & B01000000 >> 6);  //CZ7
  sensorReadings[7] = !(PINC >> 7 & B10000000 >> 7);  //CZ8
  sensorReadings[8] = !(PINA >> 7 & B10000000 >> 7);  //CZ9
  sensorReadings[9] = !(PINA >> 6 & B01000000 >> 6);  //CZ10
  sensorReadings[10] = !(PINA >> 5 & B00100000 >> 5); //CZ11
  sensorReadings[11] = !(PINA >> 4 & B00010000 >> 4); //CZ12
  sensorReadings[12] = !(PINA >> 3 & B00001000 >> 3); //CZ13
  sensorReadings[13] = !(PINA >> 2 & B00000100 >> 2); //CZ14
  sensorReadings[14] = !(PINA >> 1 & B00000010 >> 1); //CZ15
  sensorReadings[15] = !(PINB & B00000001);           //CZ16
  #else
  sensorReadings[0] = (PINC & B00000001);            //CZ1
  sensorReadings[1] = (PINC >> 1 & B00000010 >> 1);  //CZ2
  sensorReadings[2] = (PINC >> 2 & B00000100 >> 2);  //CZ3
  sensorReadings[3] = (PINC >> 3 & B00001000 >> 3);  //CZ4
  sensorReadings[4] = (PINC >> 4 & B00010000 >> 4);  //CZ5
  sensorReadings[5] = (PINC >> 5 & B00100000 >> 5);  //CZ6
  sensorReadings[6] = (PINC >> 6 & B01000000 >> 6);  //CZ7
  sensorReadings[7] = (PINC >> 7 & B10000000 >> 7);  //CZ8
  sensorReadings[8] = (PINA >> 7 & B10000000 >> 7);  //CZ9
  sensorReadings[9] = (PINA >> 6 & B01000000 >> 6);  //CZ10
  sensorReadings[10] = (PINA >> 5 & B00100000 >> 5); //CZ11
  sensorReadings[11] = (PINA >> 4 & B00010000 >> 4); //CZ12
  sensorReadings[12] = (PINA >> 3 & B00001000 >> 3); //CZ13
  sensorReadings[13] = (PINA >> 2 & B00000100 >> 2); //CZ14
  sensorReadings[14] = (PINA >> 1 & B00000010 >> 1); //CZ15
  sensorReadings[15] = (PINB & B00000001);           //CZ16
  #endif
}

/**
 * @brief sends 16 sensor readouts via bluetooth in one line (eg. 0, 0, 0, 1, 1, 0, 0, 0, 0, 0, 0, 0, 0, 0, 0, 0), 
 * untill this function is selected again
 * 
 */
void LineSensors::test(){
  digitalWrite(FRONT_POWER, HIGH);
  while(!isReceived('t')){
    readSensors();
    for (int i = 0; i < 16; ++i){
      Serial.print(sensorReadings[i]);
      Serial.print(", ");
    }
    Serial.println(" ");
    delay(100);
  }
  digitalWrite(FRONT_POWER, LOW);
}

int16_t LineSensors::calculateError(){
  numOfDetectingSensors = 0; 
  weightedSumError = 0;
  for(int i = 0; i < 16; ++i){
    numOfDetectingSensors += sensorReadings[i]; // count how many sensors see the line
    weightedSumError += sensorReadings[i] * weights[i];
  }
  return error = weightedSumError / numOfDetectingSensors;
}

uint8_t LineSensors::getNumOfDetectingSensors(){
  return numOfDetectingSensors;
}

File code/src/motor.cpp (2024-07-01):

/**
 * @file motor.cpp
 * @author Dominik Workshop
 * @brief 
 * @version 0.1
 * @date 2024-03-29
 * 
 * @copyright Copyright (c) 2024
 * 
 */

#include "motor.hh"

Motor::Motor(int dirPin, int speedPin, bool reverseDirection){
  this->dirPin = dirPin;
  this->speedPin = speedPin;
  this->reverseDir = reverseDirection;
  pinMode(dirPin, OUTPUT);
  pinMode(speedPin, OUTPUT);
  setSpeed(0);
  setDirection(Forward);
}

void Motor::setSpeed(int speed){
  if (speed < 0) 
    speed = 0;
  else if (speed > 255) 
    speed = 255;
  analogWrite(this->speedPin, speed);
}

void Motor::setDirection(Direction direction){
  if(reverseDir)
    digitalWrite(dirPin, !direction);
  else
    digitalWrite(dirPin, direction);
}
